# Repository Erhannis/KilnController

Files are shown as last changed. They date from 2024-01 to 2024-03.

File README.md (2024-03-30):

Kiln controller PCB, in KiCAD.  ESP32, controlled (potentially) over wifi.

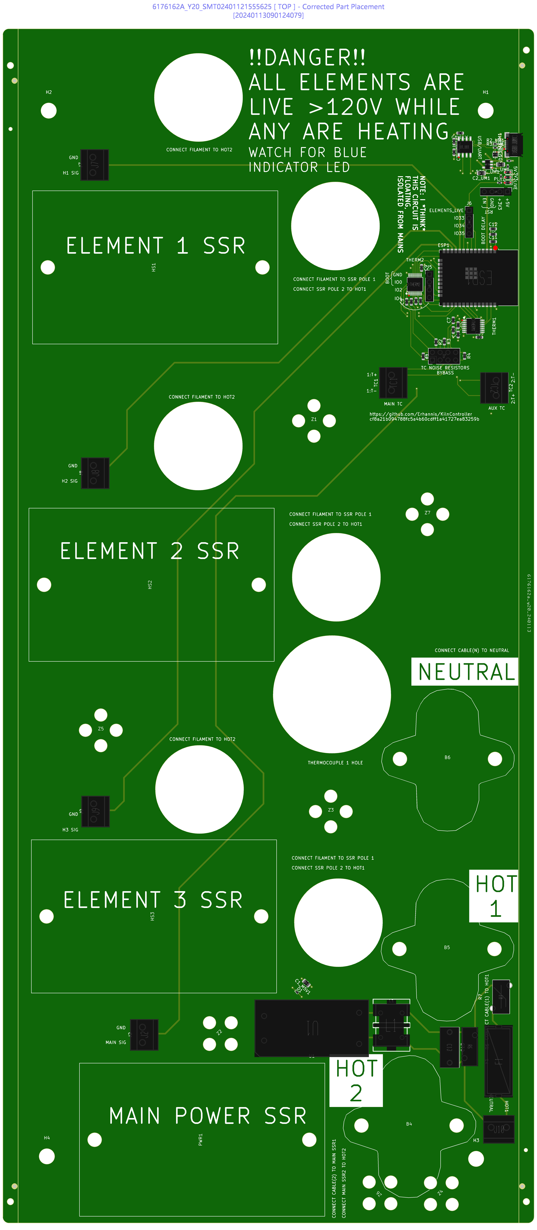
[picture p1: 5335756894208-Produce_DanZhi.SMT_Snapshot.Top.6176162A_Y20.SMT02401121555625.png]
PCB Diagram, from JLCPCB


# Instructions 
Comes with two thermocouple readers and controls three heating elements.  Attach thermocouples to appropriate points, attach three SSR-DA60 to HEAT1-HEAT3 and another to ALL_POWER, wire in 240V (see instructions on board), recommended don't attach USB while mains voltage is connected; the 5V sources might conflict - also just seems a little unsafe.  The board is shaped to match my Everheat Classic 1210 frontplate - hopefully it fits, haha.  You can reshape it if you want, or just run wires to your thermocouples and elements.  The Main TC is for inside the kiln (PIDKiln has a link to a sturdy thermocouple), the Aux TC is for the kiln outside surface (I think it's optional?).  I broke out all 6 unused GPIO pins.  See [code](#code) for firmware.

Warning: if any elements are active, all elements are live at >= 120V.  There's a blue LED that lights up when any element is active; watch out for the blue LED.  ALSO!  I hear that SSRs can fail closed, meaning the elements may stay live even once the blue LED turns off.  So...maybe just unplug the thing if you're gonna touch the coils.

# Code
See my fork of PIDKiln at https://github.com/erhannis/PIDKiln
Note that in order to flash the code, the board must be unpowered to start, you need to connect BOOT to GND, plug the board in via USB, and then you have a handful of seconds to initiate a data transfer at 115200 baud (either the main code flashing, or the "ESP32 Sketch Data Upload").  Try turning on Arduino IDE logs for compilation and upload, then copy the relevant upload command into the terminal, for timing.  Afterward, remove boot jumper and replug the board.

Disclaimer: I have no formal electronics training, and this thing connects to 240V, so like, maybe use this thing away from anything flammable, and on your own head be the results.  And DON'T TOUCH THE COILS WHILE IT'S HEATING!  Because they're live 240V, and also may be hot.

# Additional parts
Thermocouple: https://www.auberins.com/index.php?main_page=product_info&cPath=20_3&products_id=39
  (Also one of the cheap k-type thermocouples from amazon, for the case.  Though, see notes.)
Bus blocks: https://www.amazon.com/dp/B0B2L7QBVN
Heat sinks: https://www.amazon.com/dp/B08ZCYBPTV
SSRs: https://www.amazon.com/dp/B01MSTFKIP (60DA)
  Note that (according to tests) these start and stop conducting at zero volt crossings.  Also, they still let like 2mA through while open, which CAN yield high voltages.
  You might get away with lower amp ones.

# Notes
I picked the slightly more expensive thermocouple readers, which (supposedly) are more accurate and support multiple thermocouple types instead of just K - just in case that turns out to be useful.  If you're not using k-type, though, you'll probably need to tweak something in code to tell the controllers so.
I had trouble where at high temperatures, the readings on both thermocouples would go nuts.  This stopped happening after I hung the case thermocouple away from contact with anything else.  I am baffled as to how that could have happened.

MIT license.

-Erhannis

Btw, I have like 4 extra from the manufacturing batch if anybody want to buy one for like, I dunno, $100, say.  (You'll have to add the SSRs and bus terminals yourself, though.)  Getting 5 boards assembled from JLCPCB costs around $330 total.
(If you're up for soldering the ESP32 WROOM module yourself (difficult), you can use Economy mode instead of Standard and save like $100.)

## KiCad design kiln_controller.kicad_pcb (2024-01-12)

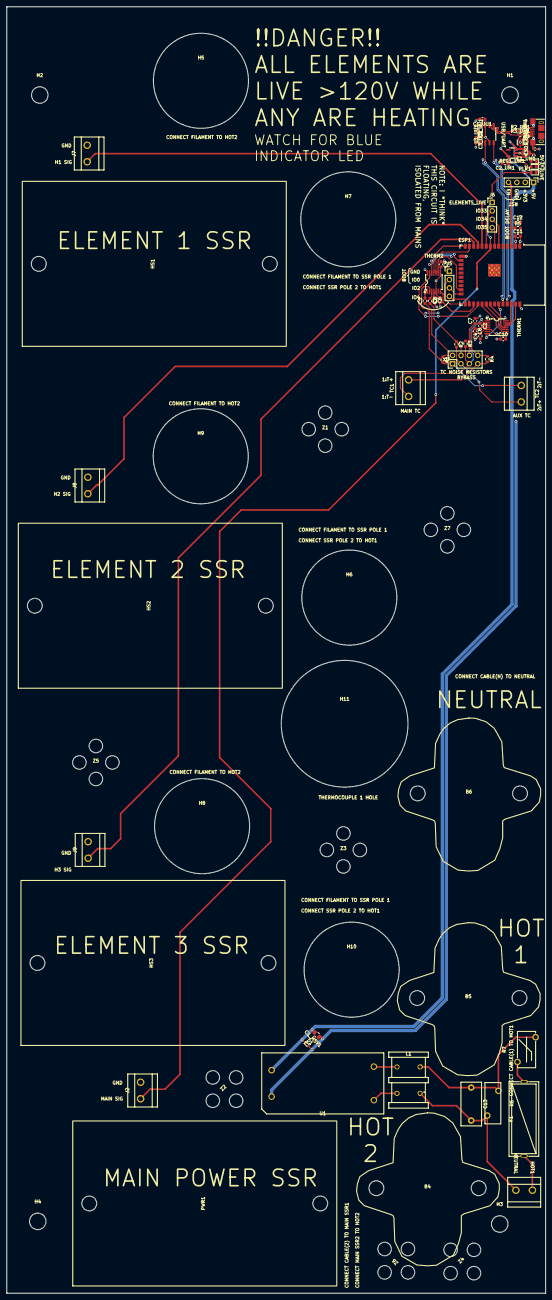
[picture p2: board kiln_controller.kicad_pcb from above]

Board: 4 copper layers, 163.3 x 389.8 mm, 82 parts (0 on the bottom side), 51 nets.

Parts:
B4, B5, B6: bus_stud
C1, C2, C3, C4, C9, C10: 100nF; C_0603_1608Metric
C1_M5V1, C1_UM1, C2_UM1: 10uF; C_0805_2012Metric
C1_UU1, C2_UU1, C3_UU1, C12: 1uF; C_0603_1608Metric
C5, C6, C7, C8: 10nF; C_0603_1608Metric
C11: 22uF; C_0603_1608Metric
C13: 100nF/275V; C_Rect_L13.0mm_W6.0mm_P10.00mm_FKS3_FKP3_MKS4
D1: ESD9B5.0ST5G; D_SOD-923
D1_UM1: LED(R); LED_0603_1608Metric
D2_UM1: LED(G); LED_0603_1608Metric
ESD1_UM1: USBLC6-2P6; SOT-666
ESP1: ESP32-WROOM-32D
F1: Fuse transparent seat; FUSE-TH_L24.5-W9.8-P22.5
H1, H2, H3, H4: MountingHole; MountingHole_5mm
H5, H6, H7, H8, H9, H10: MountingHole; MountingHole_6mm
H11: MountingHole; MountingHole_6.5mm
HS1, HS2, HS3: SSR Heat Sink
J1: Conn_02x04_Row_Letter_First; PinHeader_2x04_P2.54mm_Vertical
J2, J7, J8, J9, J10: XY126V-5.0-2P; CONN-TH_XY126V-5.0-2P
J4, J5, J6: Conn_01x04_Pin; PinHeader_1x04_P2.54mm_Vertical
L1: UU9.8-20MH; FILTER-TH_4P-L17.0-W12.0-P7.00-D0.6-S8.00
PLED1: LED(B); LED_0603_1608Metric
PLR1: 330; R_0402_1005Metric
PWR1: SSR Heat Sink
R1, R2, R3, R4: 100Ω; R_0603_1608Metric
R1_UM1: 1M; R_0402_1005Metric
R2_UM1, R3_UM1: 27; R_0402_1005Metric
R4_UM1, R5_UM1: 330; R_0402_1005Metric
R5: 10k; R_0603_1608Metric
R6: 471KD10; RES-TH_L12.5-W4.8-P7.50-D1.2-S3.40
R7: 5D-9_C332361; RES-TH_L11.0-W5.5-P7.50-D0.8-S5.50
REG1_UM1: AP2112K-3.3; SOT-23-5
TC1, TC2: XY126V-5.0-2P; CONN-TH_XY126V-5.0-2P
THERM1, THERM2: MAX31856MUD+T; TSSOP-14_L5.0-W4.4-P0.65-LS6.4-BL
U1: EC03-S05_C2840800; PWRM-TH_EC03-S05
U1_UU1: HT42B534_8SOP; SOP-8_3.9x4.9mm_P1.27mm
USB1_UM1: USB_B_Micro; USB_Micro-B_XKB_U254-051T-4BH83-F1S
Z1, Z2, Z3, Z4, Z5, Z6, Z7: zip_tie_big

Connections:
+3V3: C1_UU1.1, C2_UM1.1, C3.2, C3_UU1.1, C4.2, C9.2, C10.2, C11.1, ESP1.2 (VDD), J4.2, R5.2, R5_UM1.1, REG1_UM1.5 (VOUT), THERM1.5 (AVDD), THERM1.8 (DVDD), THERM2.5 (AVDD), THERM2.8 (DVDD), U1_UU1.3 (VDDIO), U1_UU1.7 (VDD)
+5V: C1_M5V1.2, C1_UM1.1, D1.1 (A1), ESD1_UM1.5 (VBUS), J4.1, R4_UM1.1, REG1_UM1.1 (VIN), REG1_UM1.3 (EN), U1.5 (+Vo), USB1_UM1.1 (VBUS)
/EN: C12.1, ESP1.3 (EN), J4.4, R5.1
/USB Micro B/USB D+: R2_UM1.1, U1_UU1.5 (D+)
/USB Micro B/USB D-: R3_UM1.1, U1_UU1.6 (D-)
/USB-UART/RX: ESP1.35 (TXD0/IO1), U1_UU1.4 (RX)
/USB-UART/TX: ESP1.34 (RXD0/IO3), U1_UU1.2 (TX)
ALL_POWER: ESP1.8 (IO32), J2.1, J6.1, PLR1.1
GND: C1_M5V1.1, C1_UM1.2, C1_UU1.2, C2_UM1.2, C2_UU1.2, C3.1, C3_UU1.2, C4.1, C5.2, C6.2, C7.2, C8.2, C9.1, C10.1, C11.2, C12.2, D1.2 (A2), D1_UM1.1 (K), D2_UM1.1 (K), ESD1_UM1.2 (GND), ESP1.1 (GND), ESP1.15 (GND), ESP1.38 (GND), ESP1.39 (GND), J2.2, J4.3, J5.1, J7.2, J8.2, J9.2, PLED1.1 (K), R1_UM1.1, REG1_UM1.2 (GND), THERM1.1 (AGND), THERM1.14 (DGND), THERM2.1 (AGND), THERM2.14 (DGND), U1.3 (-Vo), U1_UU1.1 (GND), USB1_UM1.5 (GND)
HEAT1: ESP1.10 (IO25), J7.1
HEAT2: ESP1.11 (IO26), J8.1
HEAT3: ESP1.12 (IO27), J9.1
unnamed: C13.1, L1.4, R6.1, R7.2
unnamed: C13.2, J10.1, L1.1, R6.2
unnamed: D1_UM1.2 (A), R4_UM1.2
unnamed: D2_UM1.2 (A), R5_UM1.2
unnamed: ESP1.25 (IO0), J5.2
unnamed: ESP1.24 (IO2), J5.3
unnamed: ESP1.26 (IO4), J5.4
unnamed: ESP1.29 (IO5), THERM1.9 (~CS)
unnamed: ESP1.14 (IO12), THERM2.11 (SDO)
unnamed: ESP1.16 (IO13), THERM2.12 (SDI)
unnamed: ESP1.13 (IO14), THERM2.10 (SCK)
unnamed: ESP1.23 (IO15), THERM2.9 (~CS)
unnamed: ESP1.27 (IO16), THERM2.7 (~DRDY)
unnamed: ESP1.28 (IO17), THERM2.13 (~FAULT)
unnamed: ESP1.30 (IO18), THERM1.10 (SCK)
unnamed: ESP1.31 (IO19), THERM1.11 (SDO)
unnamed: ESP1.33 (IO21), THERM1.7 (~DRDY)
unnamed: ESP1.36 (IO22), THERM1.13 (~FAULT)
unnamed: ESP1.37 (IO23), THERM1.12 (SDI)
unnamed: ESP1.9 (IO33), J6.2
unnamed: ESP1.6 (IO34), J6.3
unnamed: ESP1.7 (IO35), J6.4
unnamed: F1.1, J10.2
unnamed: F1.2, R7.1
unnamed: J1.1, R1.2, TC2.1, THERM2.2 (BIAS)
unnamed: C1.1, C5.1, J1.2, R1.1, THERM2.3 (T-)
unnamed: J1.3, R2.2, TC2.2
unnamed: C1.2, C6.1, J1.4, R2.1, THERM2.4 (T+)
unnamed: J1.5, R3.2, TC1.1, THERM1.2 (BIAS)
unnamed: C2.1, C7.1, J1.6, R3.1, THERM1.3 (T-)
unnamed: J1.7, R4.2, TC1.2
unnamed: C2.2, C8.1, J1.8, R4.1, THERM1.4 (T+)
unnamed: PLED1.2 (A), PLR1.2
unnamed: L1.3, U1.1 (AC(L))
unnamed: L1.2, U1.2 (AC(N))
unnamed: C2_UU1.1, U1_UU1.8 (V33O)
unnamed: ESD1_UM1.1 (I/O1), ESD1_UM1.6 (I/O1), R2_UM1.2, USB1_UM1.3 (D+)
unnamed: ESD1_UM1.3 (I/O2), ESD1_UM1.4 (I/O2), R3_UM1.2, USB1_UM1.2 (D-)
unnamed: R1_UM1.2, USB1_UM1.6 (Shield)

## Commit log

2024-01-09 Kiln controller. Probably should have committed before now. Nearly done with the schematic.
    [kiln_controller.kicad_pcb, kiln_controller.kicad_sch, usb_micro_b.kicad_sch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]
2024-01-09 Comments etc. Also added mains power module.
    [kiln_controller.kicad_sch]
2024-01-09 Working on pcb
    [kiln_controller.kicad_pcb]
2024-01-10 Added warning. Also added some footprints of larger hardware, and laid out the board shape.
    [kiln_controller.kicad_pcb, kiln_controller.kicad_sch]
2024-01-10 Board mostly laid out
    [kiln_controller.kicad_pcb, kiln_controller.kicad_sch]
2024-01-11 Decided to add a safety relay. This meant swapping for smaller bus blocks.
    [general_layout.kicad_sch, kiln_controller.kicad_pcb, kiln_controller.kicad_sch]
2024-01-11 Nearing completion
    [kiln_controller.kicad_pcb]
2024-01-11 Tweaks and stuff. I think it's about ready?
    [kiln_controller.kicad_pcb]
2024-01-12 Ok, DRC passes (basically)
    [kiln_controller.kicad_pcb]
2024-01-12 Updated power module for filtering and tvs etc.
    [kiln_controller.kicad_pcb, kiln_controller.kicad_sch, usb_uart.kicad_sch]
2024-01-12 Added blue danger LED. Passes ERC.
    [kiln_controller.kicad_pcb, kiln_controller.kicad_sch, usb_micro_b.kicad_sch]
2024-01-12 Also passes DRC
    [kiln_controller.kicad_pcb]
2024-01-12 Eh, the esp32 gnd pad vias were smaller than the jlcpcb default minimum
2024-01-12 Ahh, heck; I accidentally added an LED with only 1 in stock
2024-01-12 Oops, didn't hit save, I guess
    [kiln_controller.kicad_sch]
2024-03-30 Argh, I forgot to stage readme
2024-03-30 Fixed source
    [kiln_controller.kicad_sch]

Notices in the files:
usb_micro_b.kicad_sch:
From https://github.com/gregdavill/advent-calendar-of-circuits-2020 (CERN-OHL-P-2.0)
